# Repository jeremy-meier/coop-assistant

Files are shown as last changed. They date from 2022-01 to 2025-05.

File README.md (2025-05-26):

# Coop Assistant
An ESPHome based automatic chicken coop door integrated with Home Assistant

The Coop Assistant project has the following features:
* Integrated DHT22 temperature and humidity sensor
* Integrated VEML7700 ambient light sensor to enable automatic open/close of coop door
* Two inputs for reed relay door sensors - I use these for the nesting box and larger door in our coop
* Motor drive output for controlling a smaller door ('chicken door') via a linear actuator
  * This is integrated with Home Assisstant using a Cover component.  The ADS1115 Analog to Digital converter senses current in each leg of the H-bridge drive to determine when the door is closed.
  * Home Assistant can be used to configure manual operation of the chicken door, or automatic mode can be used to determine the lighting level when the door should be opened or closed.
* Output for connecting a 12V LED strip for coop lighting
* Inputs for connecting switches for manual Open/Close/Stop operations

See https://github.com/jeremy-meier/coop-assistant for additional documentation.

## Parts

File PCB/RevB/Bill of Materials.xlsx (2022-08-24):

Part | Value | Device | Package | Description | CATEGORY | CREATED_BY | DIGIKEY_PARTNO | MANUFACTURER | MPN | OPERATING_TEMP | PACKAGE | PART_STATUS | POPULARITY | PROD_ID | RATING | ROHS_COMPLIANT | SERIES | SPICEPREFIX | SUB-CATEGORY | THERMALLOSS | TOLERANCE | TP_SIGNAL_NAME | TYPE | VALUE | VOLTAGE
C1 | 220u | CPOLRAD6.3X8 | CAPPRD250W50D630H800B | Radial Solid Polymer Aluminum Capacitors |  |  |  |  |  |  |  |  |  |  |  |  |  |  |  |  |  |  |  |  | 16V
C2 | 100u | CPOLRAD8X12 | CAPPRD350W60D800H1200B | Kemet Radial Solid Polymer Aluminum Capacitors |  |  |  |  |  |  |  |  |  |  |  |  |  |  |  |  |  |  |  |  | 35V
C3 | 0.1u | C-EUC0805 |  | 0.1uF 100V Ceramic
C4 | 1.0uF | 1.0UF-0805-25V-10% | 805 | 1¬µF ceramic capacitors |  |  |  |  |  |  |  |  |  | CAP-08064 |  |  |  |  |  |  |  |  |  | 1.0uF
C6 | 0.1u | 1.0UF-0603-16V-10% | 603 | 1¬µF ceramic capacitors |  |  |  |  |  |  |  |  |  | CAP-00868 |  |  |  |  |  |  |  |  |  | 1.0uF
C7 | 1.0u | 1.0UF-0805-25V-10% | 805 | 1¬µF ceramic capacitors |  |  |  |  |  |  |  |  |  | CAP-08064 |  |  |  |  |  |  |  |  |  | 1.0uF
C8 | 0.1u | 1.0UF-0603-16V-10% | 603 | 1¬µF ceramic capacitors |  |  |  |  |  |  |  |  |  | CAP-00868 |  |  |  |  |  |  |  |  |  | 1.0uF
C9 | 1.0u | 1.0UF-0805-25V-10% | 805 | 1¬µF ceramic capacitors |  |  |  |  |  |  |  |  |  | CAP-08064 |  |  |  |  |  |  |  |  |  | 1.0uF
C10 | 0.1u | 1.0UF-0603-16V-10% | 603 | 1¬µF ceramic capacitors |  |  |  |  |  |  |  |  |  | CAP-00868 |  |  |  |  |  |  |  |  |  | 1.0uF
C11 | 1.0u | 1.0UF-0805-25V-10% | 805 | 1¬µF ceramic capacitors |  |  |  |  |  |  |  |  |  | CAP-08064 |  |  |  |  |  |  |  |  |  | 1.0uF
C12 | 0.1u | 1.0UF-0603-16V-10% | 603 | 1¬µF ceramic capacitors |  |  |  |  |  |  |  |  |  | CAP-00868 |  |  |  |  |  |  |  |  |  | 1.0uF
C13 | 10u | 1.0UF-0805-25V-(+80/-20%) | 805 | 1¬µF ceramic capacitors |  |  |  |  |  |  |  |  |  | CAP-11625 |  |  |  |  |  |  |  |  |  | 1.0uF
C14 | 220n | 1.0UF-0805-25V-(+80/-20%) | 805 | 1¬µF ceramic capacitors |  |  |  |  |  |  |  |  |  | CAP-11625 |  |  |  |  |  |  |  |  |  | 1.0uF
C15 | 220n | 1.0UF-0805-25V-(+80/-20%) | 805 | 1¬µF ceramic capacitors |  |  |  |  |  |  |  |  |  | CAP-11625 |  |  |  |  |  |  |  |  |  | 1.0uF
C16 | 100u | CPOLRAD8X12 | CAPPRD350W60D800H1200B | Kemet Radial Solid Polymer Aluminum Capacitors |  |  |  |  |  |  |  |  |  |  |  |  |  |  |  |  |  |  |  |  | 35V
C17 | 0.1u | 1.0UF-0603-16V-10% | 603 | 1¬µF ceramic capacitors |  |  |  |  |  |  |  |  |  | CAP-00868 |  |  |  |  |  |  |  |  |  | 1.0uF
C18 | 0.1u | 1.0UF-0603-16V-10% | 603 | 1¬µF ceramic capacitors |  |  |  |  |  |  |  |  |  | CAP-00868 |  |  |  |  |  |  |  |  |  | 1.0uF
C19 | 0.1u | 1.0UF-0603-16V-10% | 603 | 1¬µF ceramic capacitors |  |  |  |  |  |  |  |  |  | CAP-00868 |  |  |  |  |  |  |  |  |  | 1.0uF
C20 | 0.1u | C-EUC0805 | C0805 | CAPACITOR, European symbol |  |  |  |  |  |  |  |  | 88 |  |  |  |  | C
C21 | 10n | C-EUC0805 | C0805 | CAPACITOR, European symbol |  |  |  |  |  |  |  |  | 88 |  |  |  |  | C
C22 | 0.1u | 1.0UF-0603-16V-10% | 603 | 1¬µF ceramic capacitors |  |  |  |  |  |  |  |  |  | CAP-00868 |  |  |  |  |  |  |  |  |  | 1.0uF
C23 | 0.1u | 1.0UF-0603-16V-10% | 603 | 1¬µF ceramic capacitors |  |  |  |  |  |  |  |  |  | CAP-00868 |  |  |  |  |  |  |  |  |  | 1.0uF
C24 | 100u | CPOLRAD8X12 | CAPPRD350W60D800H1200B | Kemet Radial Solid Polymer Aluminum Capacitors |  |  |  |  |  |  |  |  |  |  |  |  |  |  |  |  |  |  |  |  | 35V
C26 | 1.0u | 1.0UF-0805-25V-10% | 805 | 1¬µF ceramic capacitors |  |  |  |  |  |  |  |  |  | CAP-08064 |  |  |  |  |  |  |  |  |  | 1.0uF
C27 | 1.0uF | 1.0UF-0805-25V-10% | 805 | 1¬µF ceramic capacitors |  |  |  |  |  |  |  |  |  | CAP-08064 |  |  |  |  |  |  |  |  |  | 1.0uF
C28 | 100u | CPOLRAD8X12 | CAPPRD350W60D800H1200B | Kemet Radial Solid Polymer Aluminum Capacitors |  |  |  |  |  |  |  |  |  |  |  |  |  |  |  |  |  |  |  |  | 35V
D1 | SS2FL4 | SS2FL4 | SMF | SCHOTTKY DIODE, 40V/2A
D2 | RS1A-E3/61T | DIODESMA | SMADIODE | Diode
D3 | RS1A-E3/61T | DIODESMA | SMADIODE | Diode
D4 | MBRA340T3 | MBRA340T3 | SMA | Surface Mount Schottky Power Rectifier |  |  |  |  |  |  |  |  | 9
D5 | 18V | ZENER-DIODESOT23 | SOT23 | Z-Diode |  |  |  |  |  |  |  |  | 3
F1 | 375mA | 494SERIESFUSE | 603
F3 | 3A | 154_OMNIBLOKF154 | FUSM9750X381N
IC1 | 74LVC1G06DBV | 74LVC1G06DBV | SOT23-5 | Single Inverter Buffer/Driver With Open-Drain Output |  |  |  |  |  |  |  |  | 0
IC2 | 74LVC1G06DBV | 74LVC1G06DBV | SOT23-5 | Single Inverter Buffer/Driver With Open-Drain Output |  |  |  |  |  |  |  |  | 0
L1 | 180u | MSS1278 | INDM120120X780N | SMT Power Inductors
L2 | 10uH | COILCRAFT_MSD1260 | COILCRAFT_MSD1260 | Shielded Coupled Inductors
L3 | 10u | MSS1278 | INDM120120X780N | SMT Power Inductors
LED1 |  | LEDCHIP-LED0805 | CHIP-LED0805 | LED
LED2 |  | LEDCHIP-LED0805 | CHIP-LED0805 | LED
LED3 |  | LEDCHIP-LED0805 | CHIP-LED0805 | LED
Q1 | IRFR4105 | IRFR4105 | TO252 | MOSFET 55V 1 N-CH HEXFET 45mOhms 22.7nC
Q2 | IRFR4105 | IRFR4105 | TO252 | MOSFET 55V 1 N-CH HEXFET 45mOhms 22.7nC
Q3 | IRFR4105 | IRFR4105 | TO252 | MOSFET 55V 1 N-CH HEXFET 45mOhms 22.7nC
Q4 | IRFR4105 | IRFR4105 | TO252 | MOSFET 55V 1 N-CH HEXFET 45mOhms 22.7nC
Q5 | IRFR4105 | IRFR4105 | TO252 | MOSFET 55V 1 N-CH HEXFET 45mOhms 22.7nC
Q6 | X0202MN_5BA4 | X0202MN_5BA4 | SOT-223 | SCR 600V 1.25A SOT-223
R1 | 22 | R-US_R0805 | R0805 | RESISTOR, American symbol
R2 | 1k | R-US_R0805 | R0805 | RESISTOR, American symbol
R3 | 4.7k | R-US_R0805 | R0805 | RESISTOR, American symbol
R4 | 100 | R-US_R0805 | R0805 | RESISTOR, American symbol
R5 | 1k | R-US_R0805 | R0805 | RESISTOR, American symbol
R16 | 0 | R-US_R0805 | R0805 | RESISTOR, American symbol
R17 | 1k | R-US_R0805 | R0805 | RESISTOR, American symbol
R18 | 1k | R-US_R0805 | R0805 | RESISTOR, American symbol
R19 | 0 | R-US_R0805 | R0805 | RESISTOR, American symbol
R20 | 1k | R-US_R0805 | R0805 | RESISTOR, American symbol
R21 | 1k | R-US_R0805 | R0805 | RESISTOR, American symbol
R22 | 22 | R-US_R0805 | R0805 | RESISTOR, American symbol
R23 | 10k | R-US_R0805 | R0805 | RESISTOR, American symbol
R24 | 47k | R-US_R0805 | R0805 | RESISTOR, American symbol
R25 | 4.7k | R-US_R0805 | R0805 | RESISTOR, American symbol
R26 | 50m | R-US_R2512 | R2512 | RESISTOR, American symbol
R27 | 50m | R-US_R2512 | R2512 | RESISTOR, American symbol
R28 | 4.7k | R-US_R0805 | R0805 | RESISTOR, American symbol
R29 | 4.7k | R-US_R0805 | R0805 | RESISTOR, American symbol
R30 | 1.5k | R-US_R0805 | R0805 | RESISTOR, American symbol
R31 | 1k | R-US_R0805 | R0805 | RESISTOR, American symbol
R32 | 47k | R-US_R0805 | R0805 | RESISTOR, American symbol
R33 | 100m | R-US_CHIP-1206(3216-METRIC) | RESC3216X70 | Resistor Fixed - ANSI | Resistor |  |  |  |  |  |  |  |  |  |  |  |  |  | Fixed
R34 | 1k | R-US_R0805 | R0805 | RESISTOR, American symbol
R35 | 100 | R-US_R2512 | R2512 | RESISTOR, American symbol
R39 | 0 | R-US_R0805 | R0805 | RESISTOR, American symbol
R40 | 22 | R-US_R0805 | R0805 | RESISTOR, American symbol
R41 | 22 | R-US_R0805 | R0805 | RESISTOR, American symbol
R42 | 22 | R-US_R0805 | R0805 | RESISTOR, American symbol
R43 | 22 | R-US_R0805 | R0805 | RESISTOR, American symbol
R44 | 1k | R-US_R0805 | R0805 | RESISTOR, American symbol
R45 | 1k | R-US_R0805 | R0805 | RESISTOR, American symbol
T1 | BC847 | BC847 | SOT23 | NPN TRANSISTOR |  |  |  |  |  |  |  |  | 5
T2 | BC847 | BC847 | SOT23 | NPN TRANSISTOR |  |  |  |  |  |  |  |  | 5
T3 | BC857A | BC857A | SOT23-BEC | 65 V, 100 mA PNP general-purpose transistor
TP1 | TPTP15SQ | TPTP15SQ | TP15SQ | Test pad |  |  |  |  |  |  |  |  | 0
TP2 | TPTP15SQ | TPTP15SQ | TP15SQ | Test pad |  |  |  |  |  |  |  |  | 0
TP3 | TPTP15SQ | TPTP15SQ | TP15SQ | Test pad |  |  |  |  |  |  |  |  | 0
TP4 | TPTP15SQ | TPTP15SQ | TP15SQ | Test pad |  |  |  |  |  |  |  |  | 0
TP5 | TPTP15SQ | TPTP15SQ | TP15SQ | Test pad |  |  |  |  |  |  |  |  | 0
TP6 | TPTP15SQ | TPTP15SQ | TP15SQ | Test pad |  |  |  |  |  |  |  |  | 0
TP7 | TPTP15SQ | TPTP15SQ | TP15SQ | Test pad |  |  |  |  |  |  |  |  | 0
TP8 | TPTP15SQ | TPTP15SQ | TP15SQ | Test pad |  |  |  |  |  |  |  |  | 0
TP9 | TPTP15SQ | TPTP15SQ | TP15SQ | Test pad |  |  |  |  |  |  |  |  | 0
TP10 | TPTP15SQ | TPTP15SQ | TP15SQ | Test pad |  |  |  |  |  |  |  |  | 0
TP11 | TPTP15SQ | TPTP15SQ | TP15SQ | Test pad |  |  |  |  |  |  |  |  | 0
TP12 | TPTP15SQ | TPTP15SQ | TP15SQ | Test pad |  |  |  |  |  |  |  |  | 0
TP13 | TPTP15SQ | TPTP15SQ | TP15SQ | Test pad |  |  |  |  |  |  |  |  | 0
U1 | DHT22 | RHT03_DHT-22_AM2302RA | RHT03_DHT-22/RA | RHT03 / DHT-22 / AM2302 |  |  |  |  |  |  |  |  |  | SEN-10167
U2 | ESP8266_NODEMCU | ESP8266_NODEMCU | NODEMCUESP8266 | ESP8266 NODEMCU board.
U3 | HIP4082IPZ | HIP4082IPZ | DIP762W53P254L1969H508Q16B
U4 | MIC4575-5.0WU | MIC4575-5.0WU | TO263-5 | MIC4575
U5 | LP2980AIM5-3.3 | LP2980AIM5-3.3 | SOT23-5 | Micropower 50-mA Ultra-Low-Dropout Regulator
U6 | ADS1115 | ADS1115 | HDRV10W64P254_1X10_2800X508X838B
U7 | VEML7700 | VEML7700 | VEML7700
U8 | SFH3716 | SFH3716 | 805 | Silicon NPN Phototransistor with VŒª Characteristics
U9 | ADS1115IDGST | ADS1115IDGST | 10VSSOP
X1 | MKDSN1,5/2-5,08 | MKDSN1,5/2-5,08 | MKDSN1,5/2-5,08 | MKDSN 1,5/ 2-5,08 Printklemme |  |  |  |  |  |  |  |  | 14
X2 | MKDSN1,5/8-5,08 | MKDSN1,5/8-5,08 | MKDSN1,5/8-5,08 | MKDSN 1,5/ 8-5,08 Printklemme |  |  |  |  |  |  |  |  | 1
X3 | MKDSN1,5/8-5,08 | MKDSN1,5/8-5,08 | MKDSN1,5/8-5,08 | MKDSN 1,5/ 8-5,08 Printklemme |  |  |  |  |  |  |  |  | 1
X4 | MKDSN1,5/8-5,08 | MKDSN1,5/8-5,08 | MKDSN1,5/8-5,08 | MKDSN 1,5/ 8-5,08 Printklemme |  |  |  |  |  |  |  |  | 1

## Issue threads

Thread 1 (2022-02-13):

Buck converter unstable due to insufficient ESR in output capacitor

jeremy-meier, 2022-02-13:
The MIC4575 buck controller is unstable when using the original values in the Rev A schematic.  Adding 100mOhm of ESR in series with the capacitor moves the zero lower in frequency and provides additional phase margin to make converter stable.

jeremy-meier, 2022-08-24:
R33 Added in Rev B PCB.

Closed 2022-08-24.

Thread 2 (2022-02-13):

Need additional bulk capacitance

jeremy-meier, 2022-02-13:
Some additional bulk capacitance is needed next to the H-bridge switches to help with the fast transients of turning the motor on/off.  Consider adding a couple of the 100uF caps that are already used on the buck converter input.

jeremy-meier, 2022-08-24:
C24, C16, C28 added to rev B PCB.

Closed 2022-08-24.

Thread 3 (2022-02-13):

Some additional pull up/downs needed to utilize GPIO2/GPIO15 pins

jeremy-meier, 2022-02-13:
A couple of pins are being used that need to be pulled to specific levels, otherwise the device fails to boot.  The following modifications should be made based on the following document:
https://randomnerdtutorials.com/esp8266-pinout-reference-gpio

* GPIO2/LIGHT_PWM - Needs to be pulled high otherwise the device can't boot.  Use a strong pull down, 1k should be fine.
* GPIO15/MOTOR_PWM - Needs to be pulled to ground otherwise the device can't boot.  Use a strong pull down, 1k should be fine.

jeremy-meier, 2022-08-24:
R17 & R34 added to rev B PCB.

Closed 2022-08-24.

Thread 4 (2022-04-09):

Kickback from motor turn off is triggering OVP

jeremy-meier, 2022-04-09:
When the motor turns off, the energy stored in the inductance is being pumped back onto the voltage rail, causing the OVP protection to trip.  To fix this, consider both of the following:
1. Add a snubber circuit across the motor terminals to reduce kickback
2. Put a schottky diode in series with the power feed to the output MOSFETS to prevent kickback from reaching the OVP circuit

The additional bulk capacitance on the output MOSFET power supply should also help reduce this problem.

jeremy-meier, 2022-08-24:
1. Added snubber circuit R35/C3 to rev B
2. Added schottky D6 to rev B
3. Also increased the zener voltage of D5 from 15V to 18V

Closed 2022-08-24.

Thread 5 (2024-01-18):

Use a temperature sensor capable of operating at lower temperatures

jeremy-meier, 2024-01-18:
The DHT22 temperature sensor specs say it should work down to -40C, but it doesn't seem like that's the case.  The sensor is reporting -5000 degrees in home assistant when the temperature drops below freezing.  However humidity seems fine.  Consider using a different temperature sensor.

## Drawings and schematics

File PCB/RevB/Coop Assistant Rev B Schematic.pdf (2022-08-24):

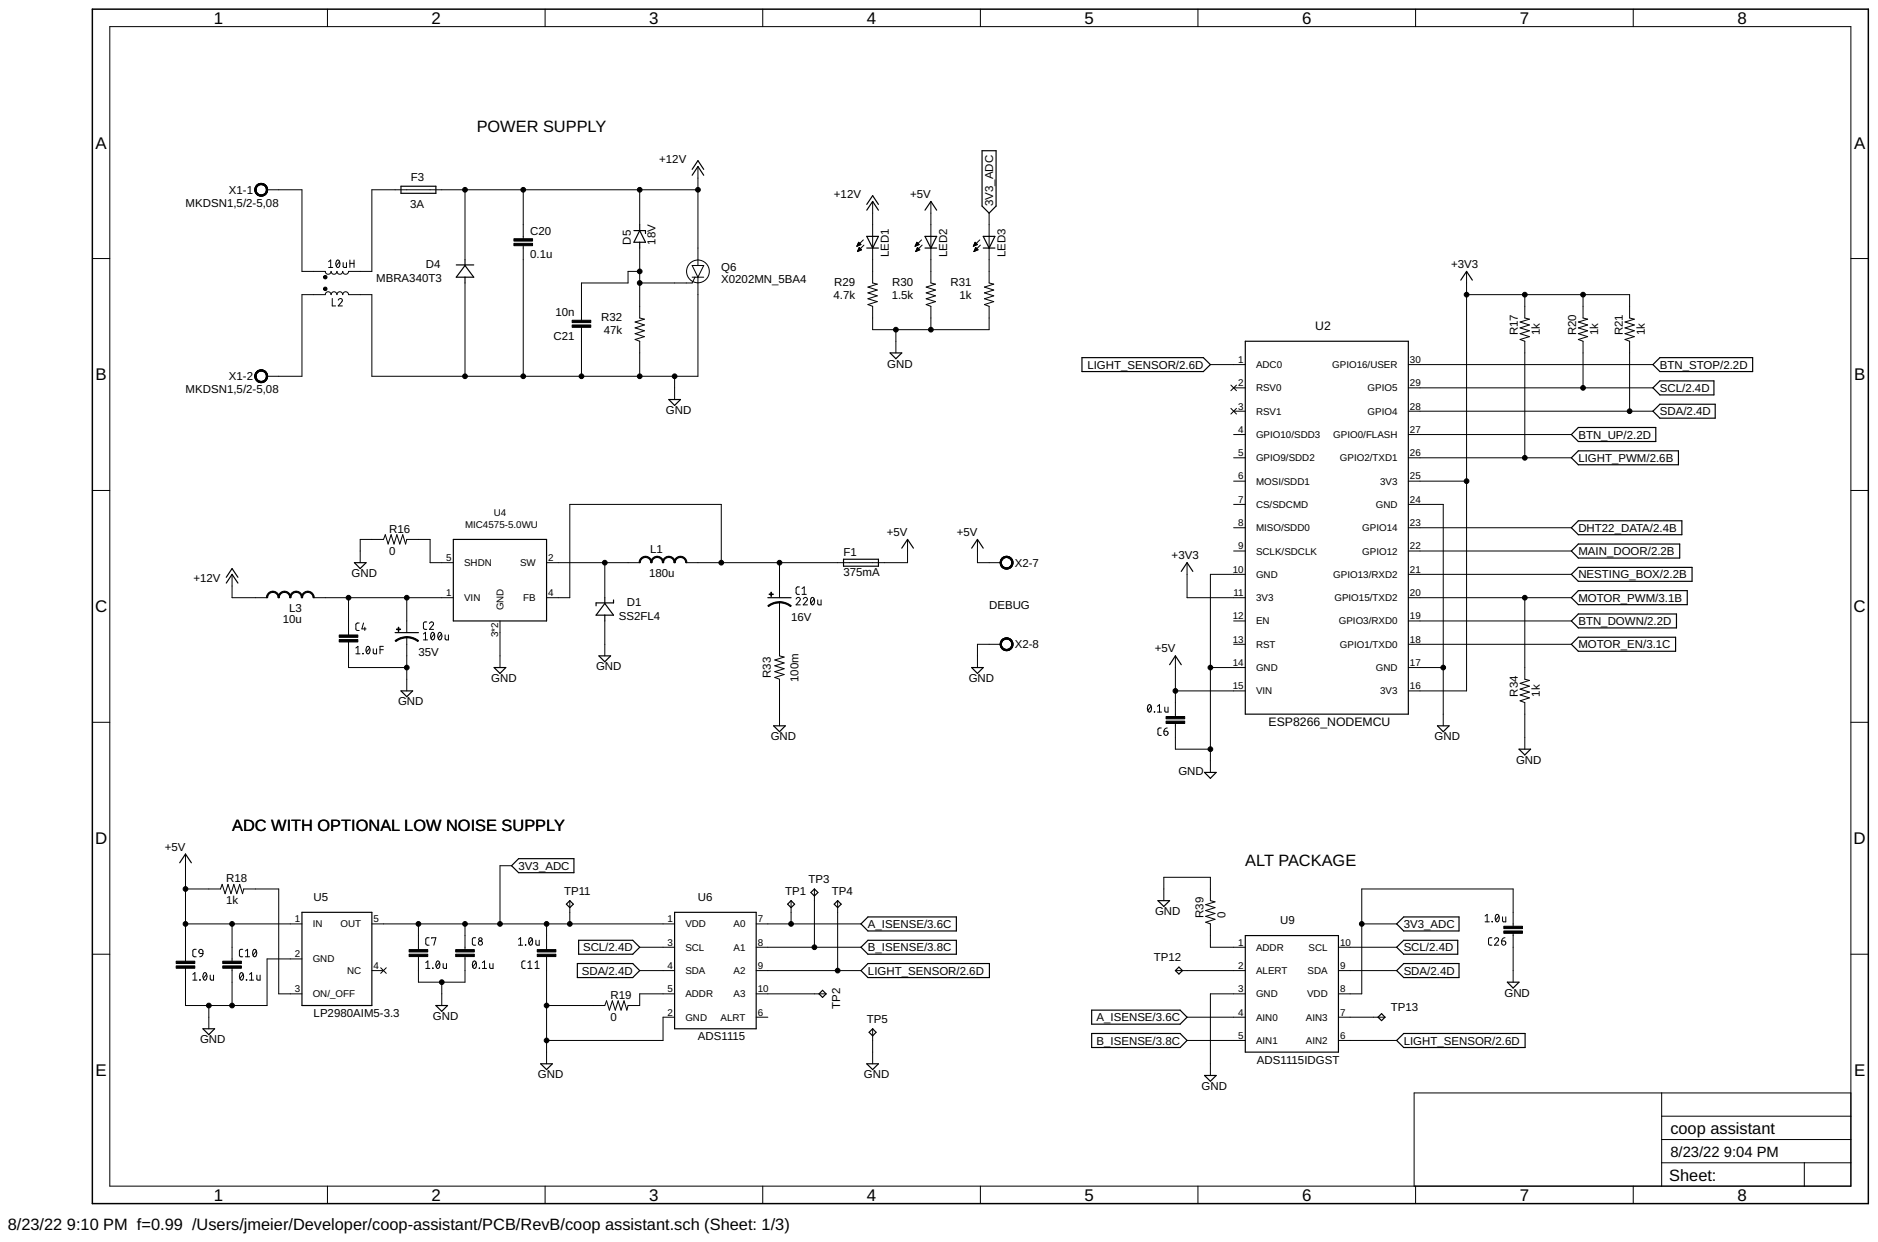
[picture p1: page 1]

ADC WITH OPTIONAL LOW NOISE SUPPLY

8/23/22 9:10 PM f=0.99 /Users/jmeier/Developer/coop-assistant/PCB/RevB/coop assistant.sch (Sheet: 1/3)

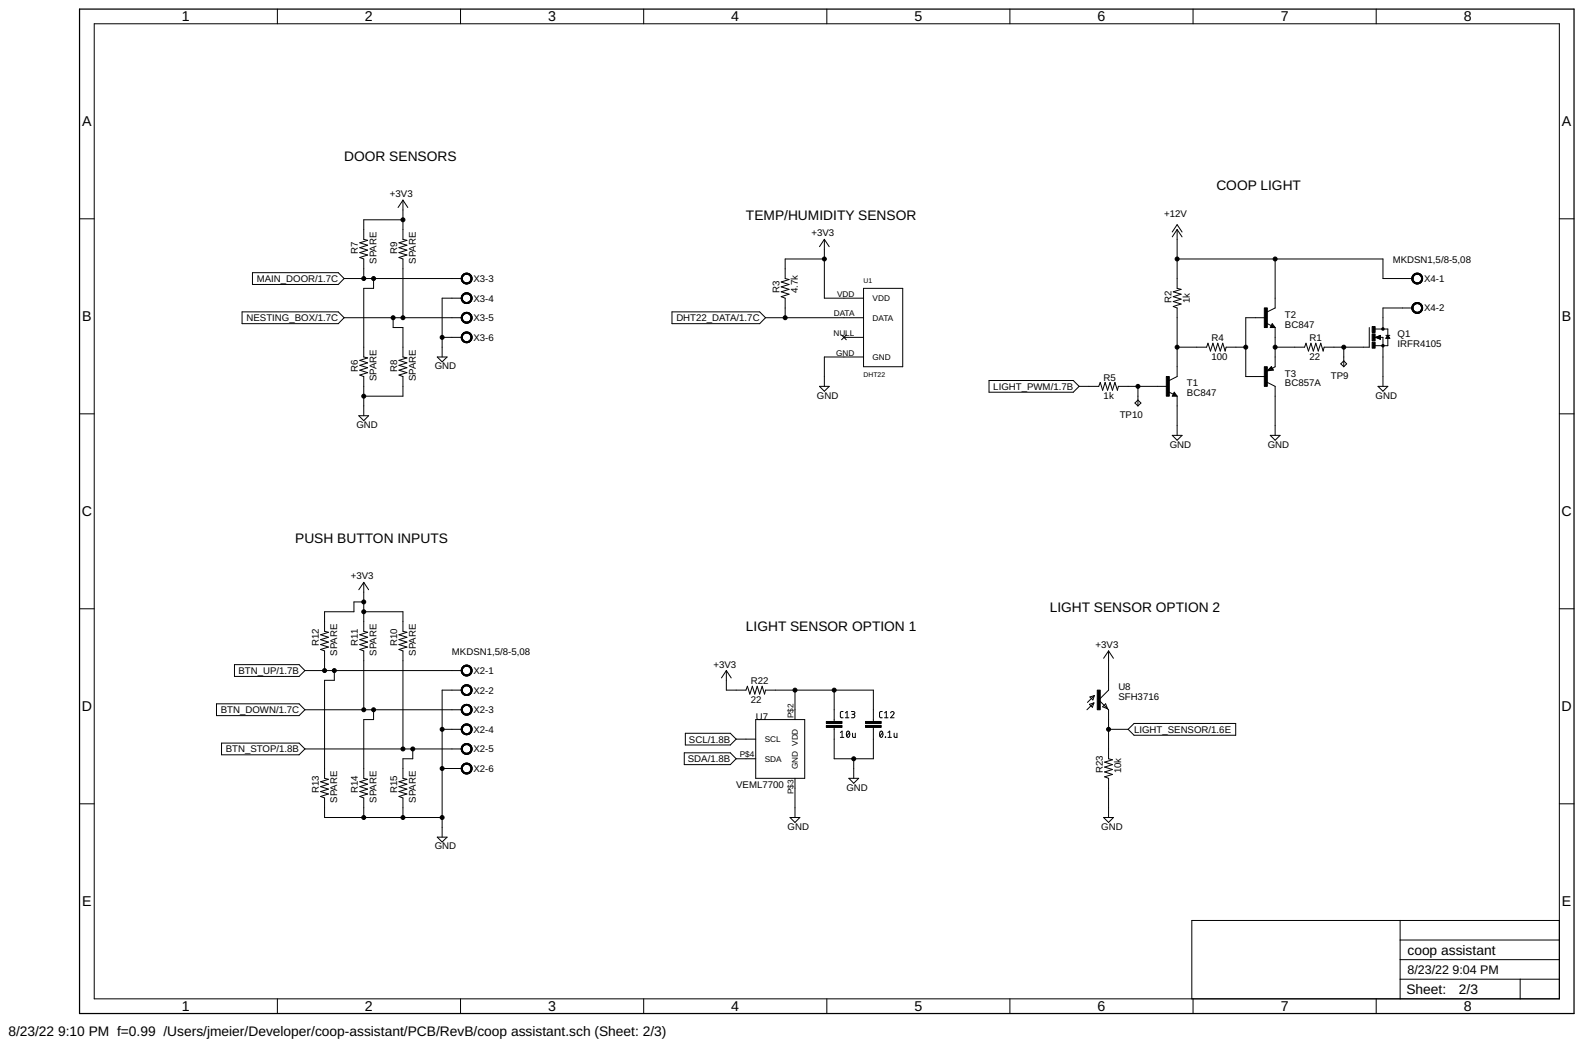
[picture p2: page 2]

8/23/22 9:10 PM f=0.99 /Users/jmeier/Developer/coop-assistant/PCB/RevB/coop assistant.sch (Sheet: 2/3)

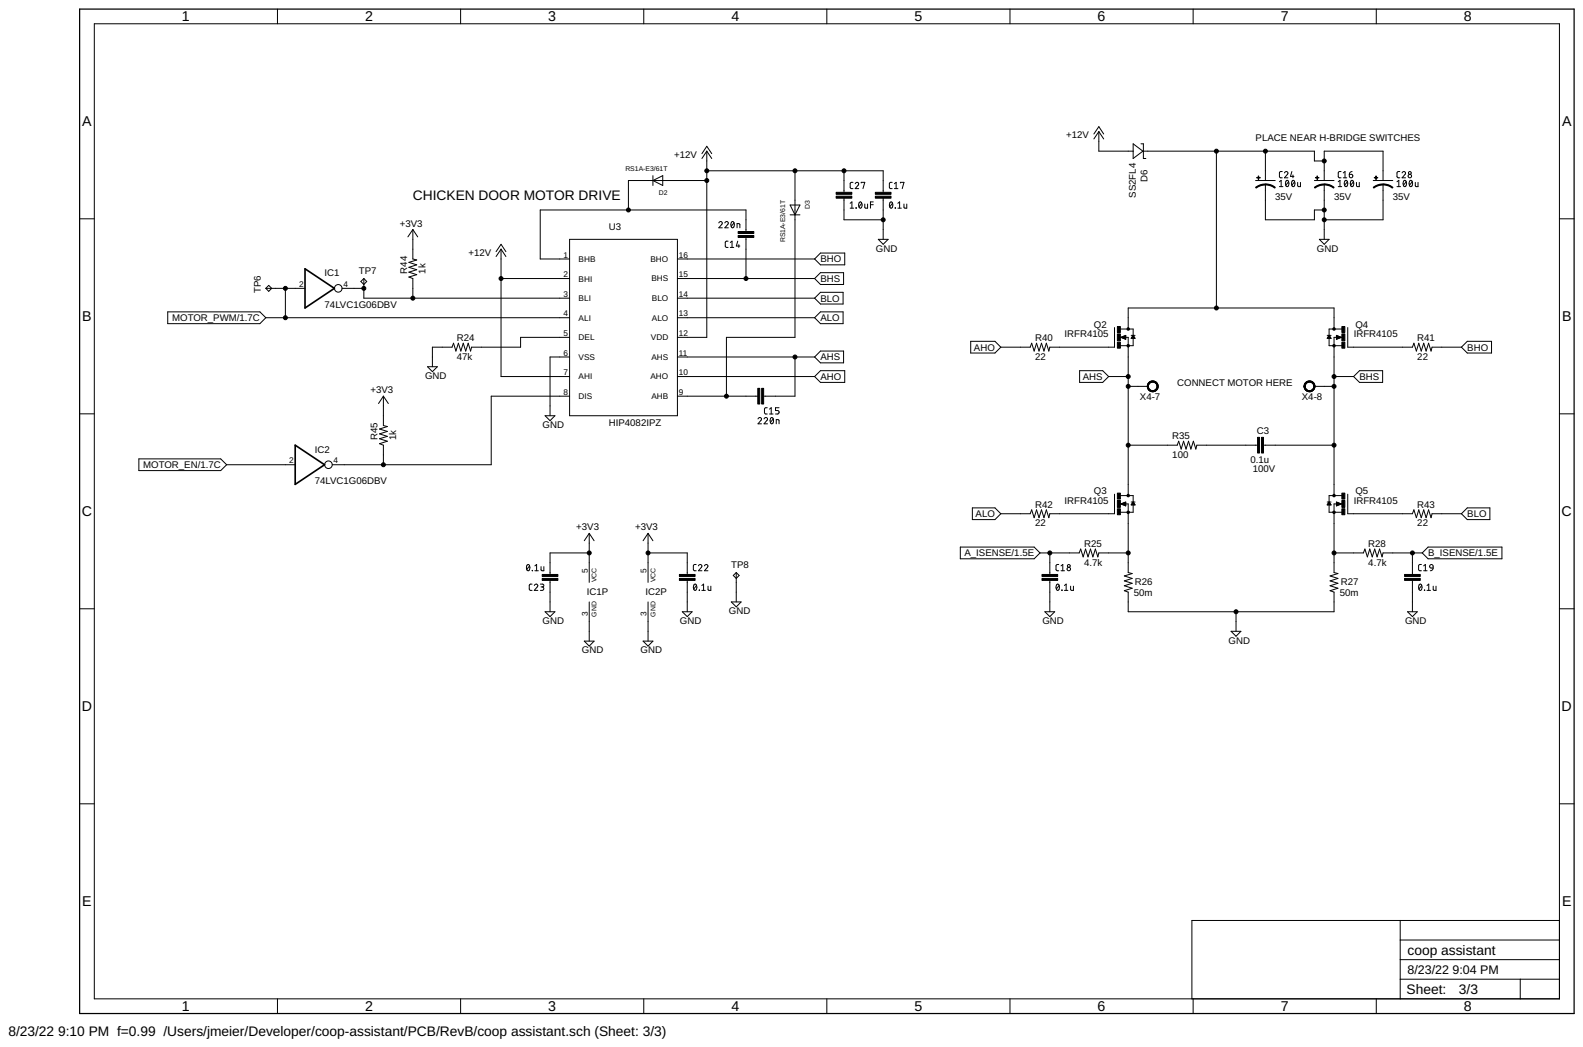
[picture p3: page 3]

PLACE NEAR H-BRIDGE SWITCHES

CHICKEN DOOR MOTOR DRIVE

8/23/22 9:10 PM f=0.99 /Users/jmeier/Developer/coop-assistant/PCB/RevB/coop assistant.sch (Sheet: 3/3)

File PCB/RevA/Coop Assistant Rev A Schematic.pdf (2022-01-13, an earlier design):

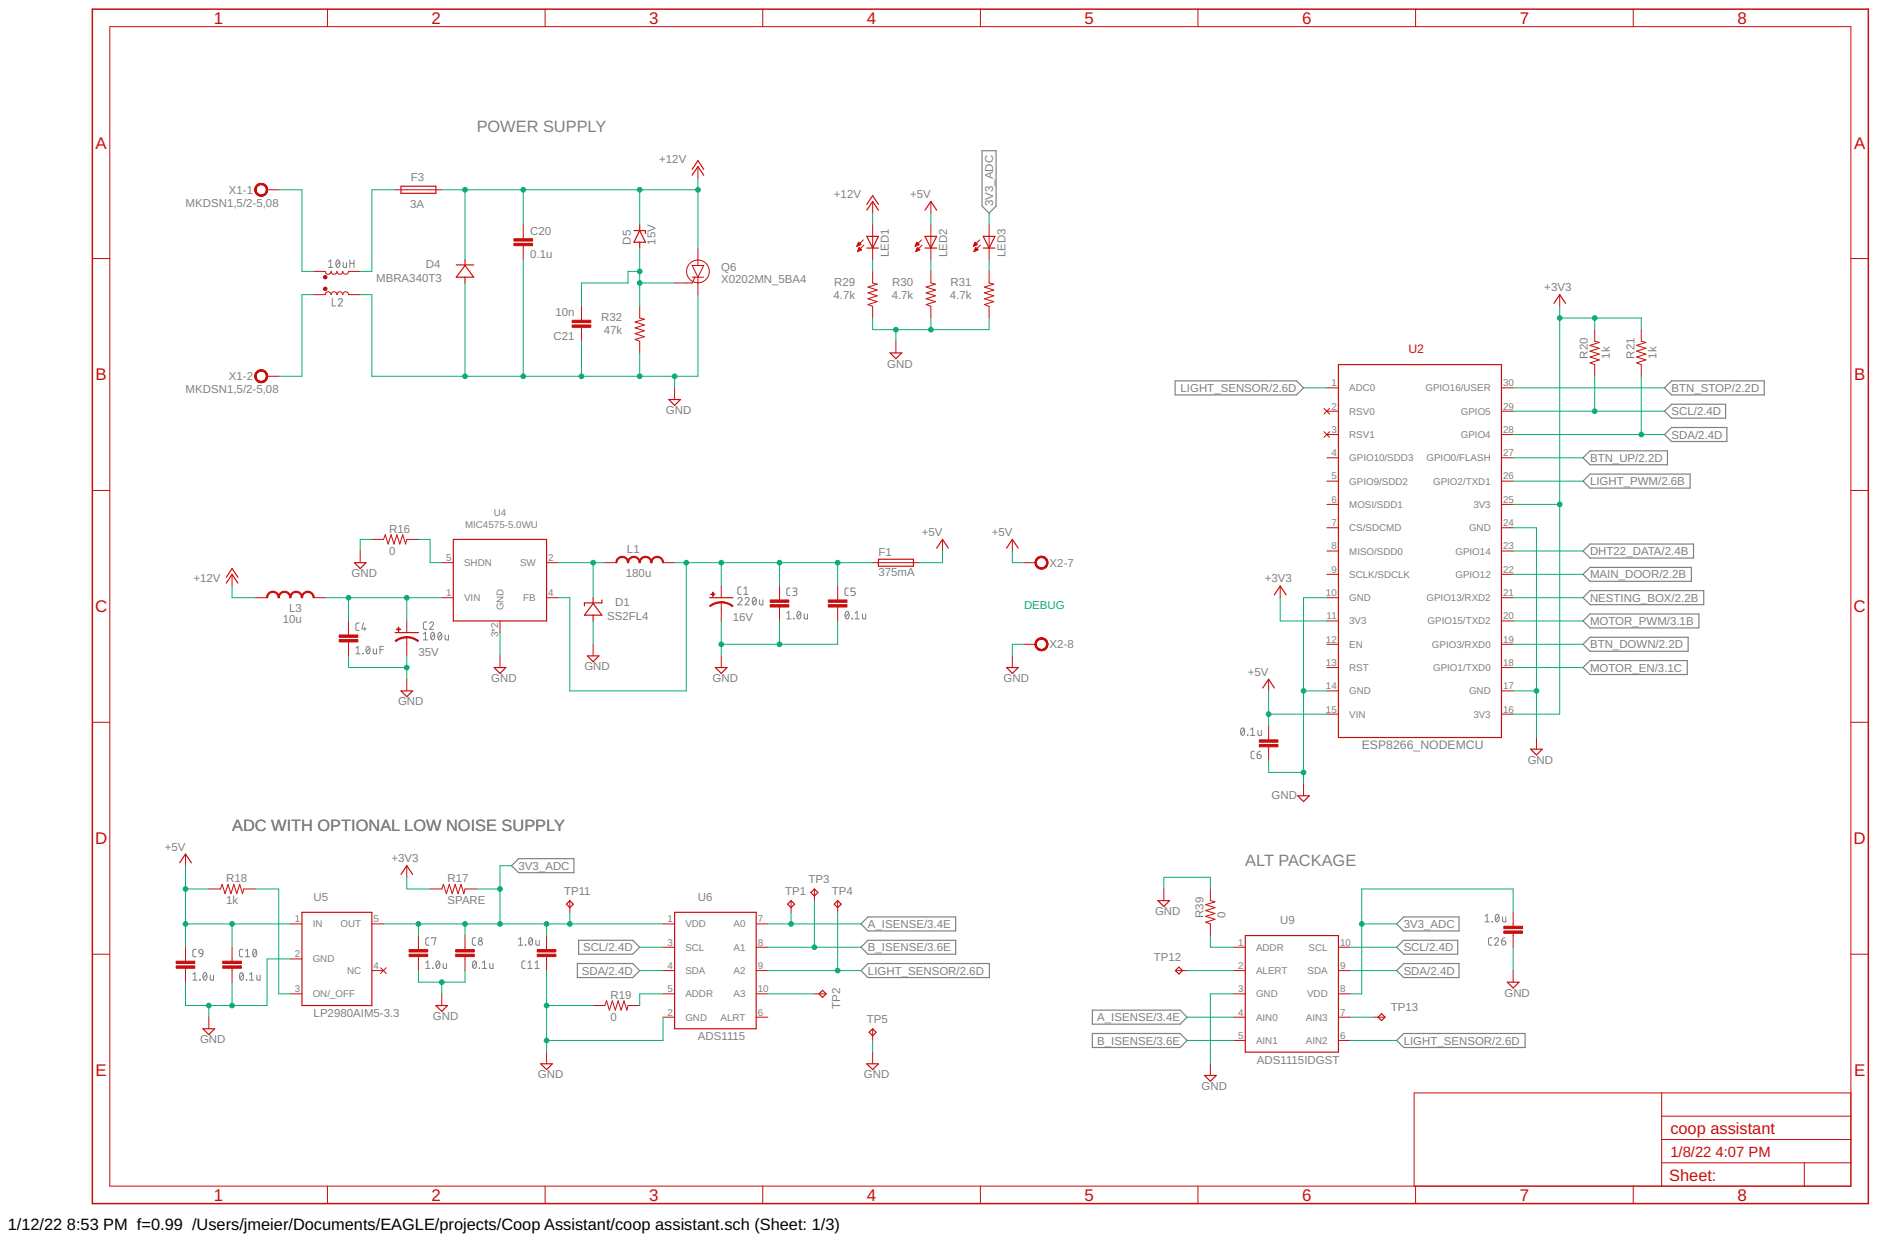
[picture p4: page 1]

ADC WITH OPTIONAL LOW NOISE SUPPLY

1/12/22 8:53 PM f=0.99 /Users/jmeier/Documents/EAGLE/projects/Coop Assistant/coop assistant.sch (Sheet: 1/3)

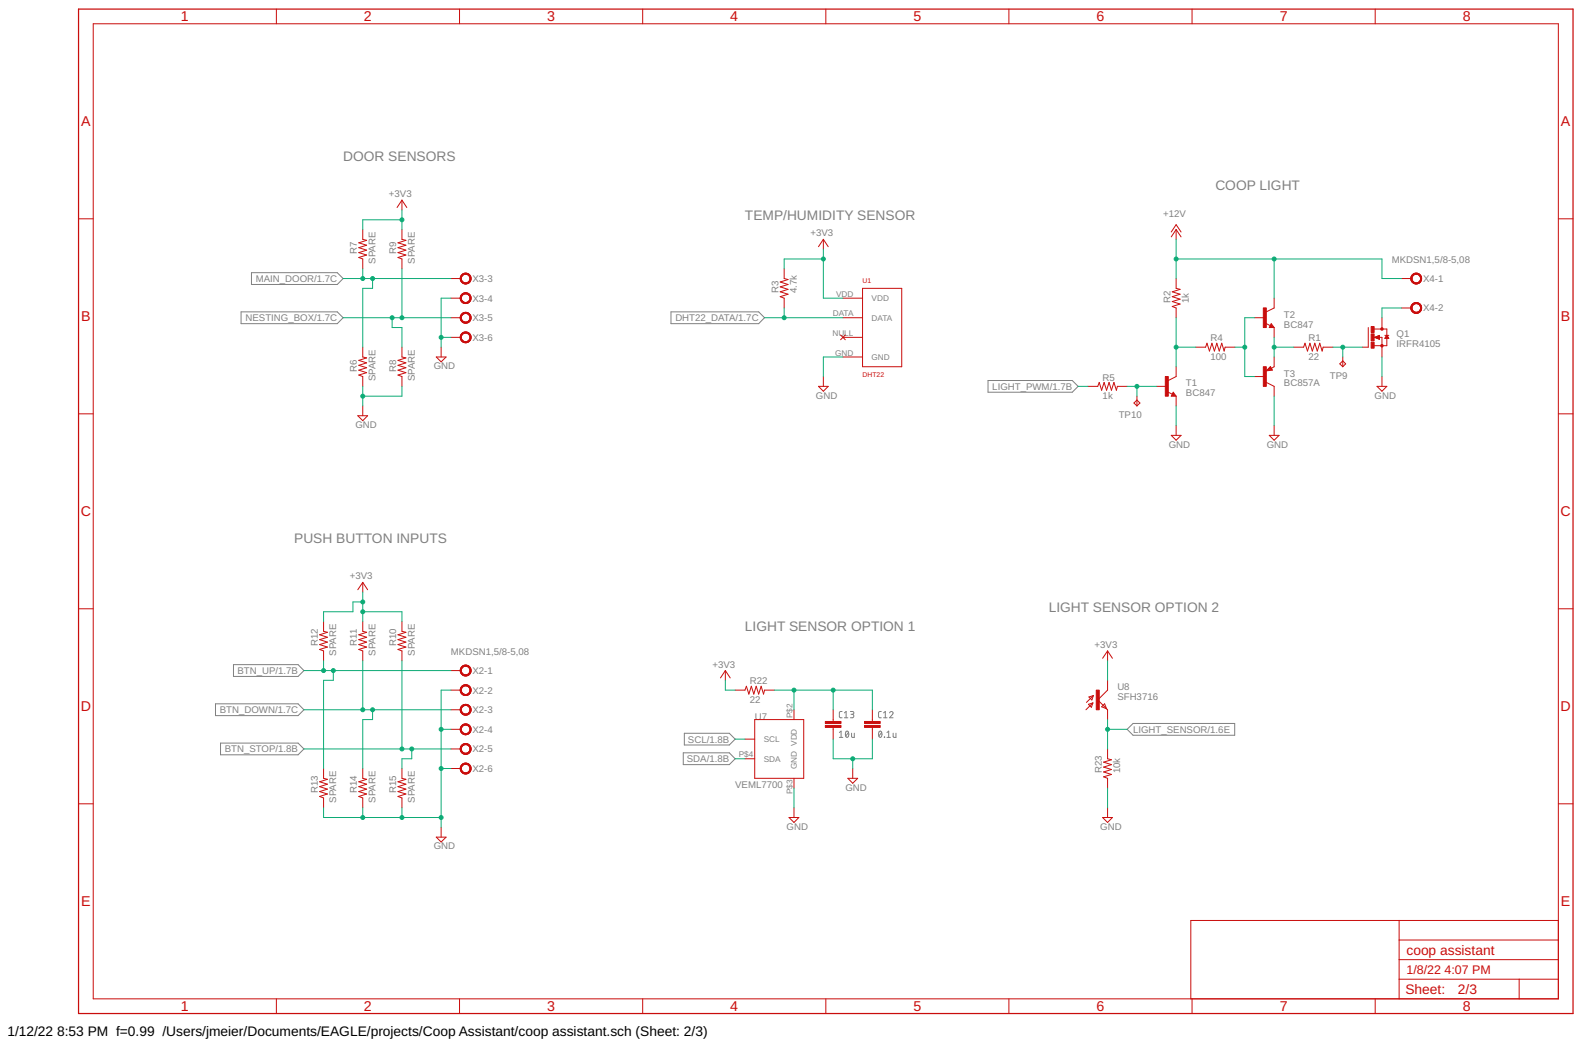
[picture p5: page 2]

1/12/22 8:53 PM f=0.99 /Users/jmeier/Documents/EAGLE/projects/Coop Assistant/coop assistant.sch (Sheet: 2/3)

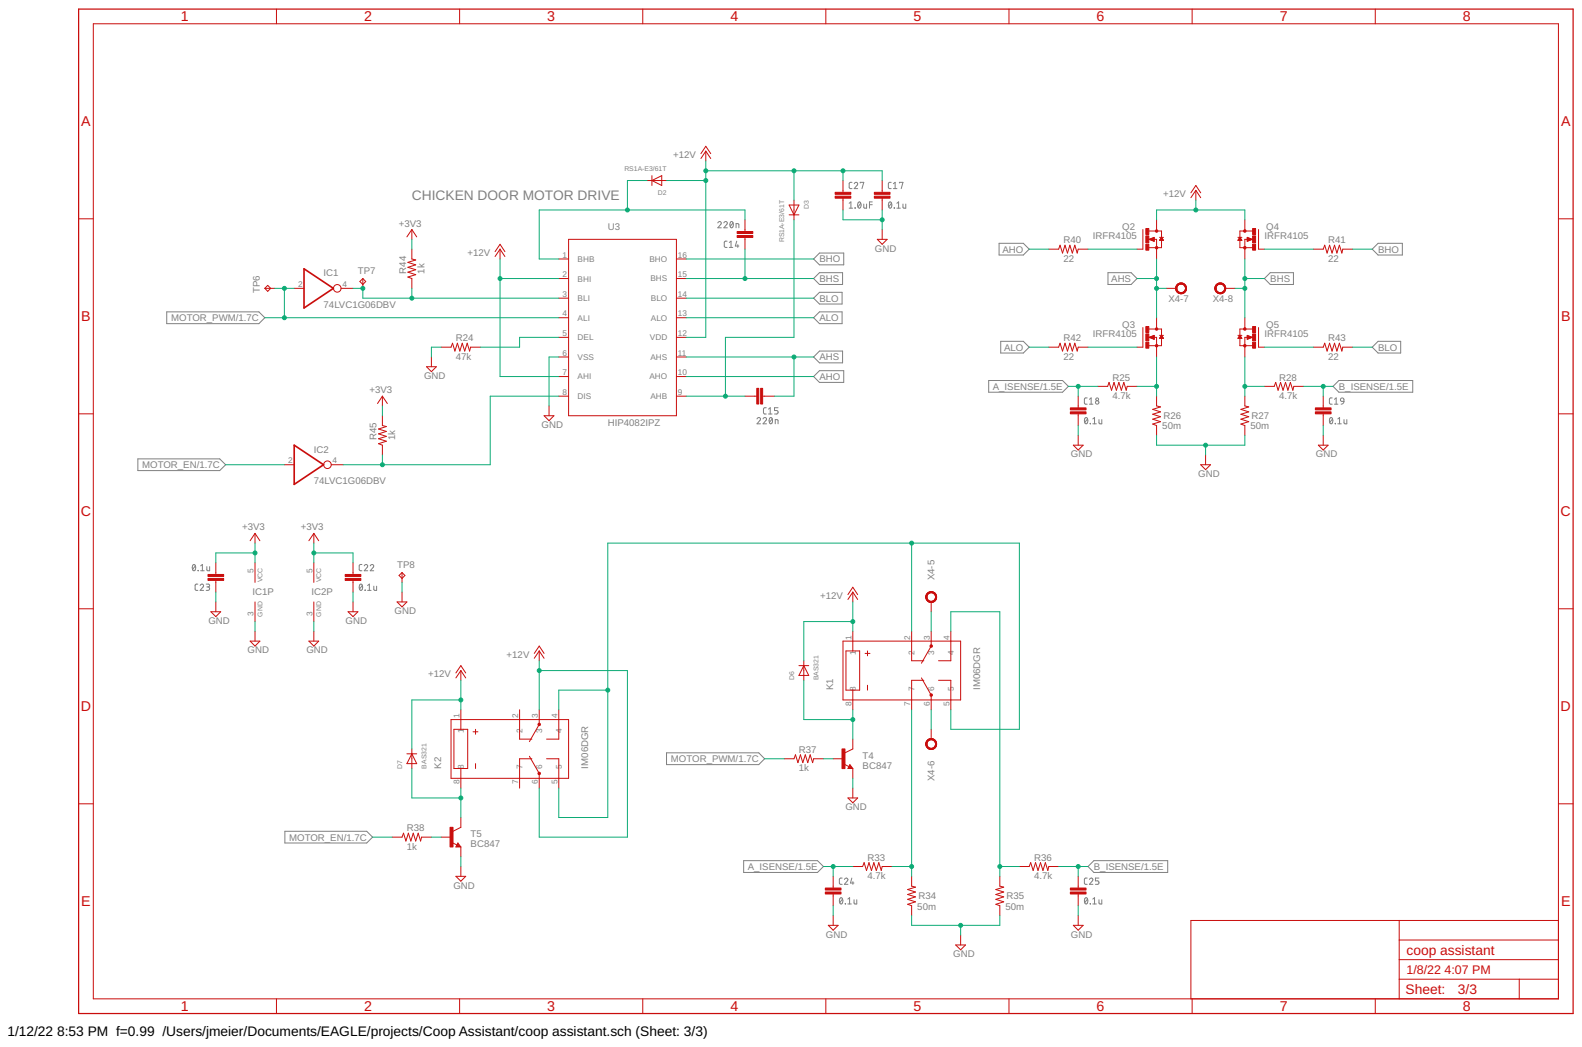
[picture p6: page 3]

CHICKEN DOOR MOTOR DRIVE

1/12/22 8:53 PM f=0.99 /Users/jmeier/Documents/EAGLE/projects/Coop Assistant/coop assistant.sch (Sheet: 3/3)

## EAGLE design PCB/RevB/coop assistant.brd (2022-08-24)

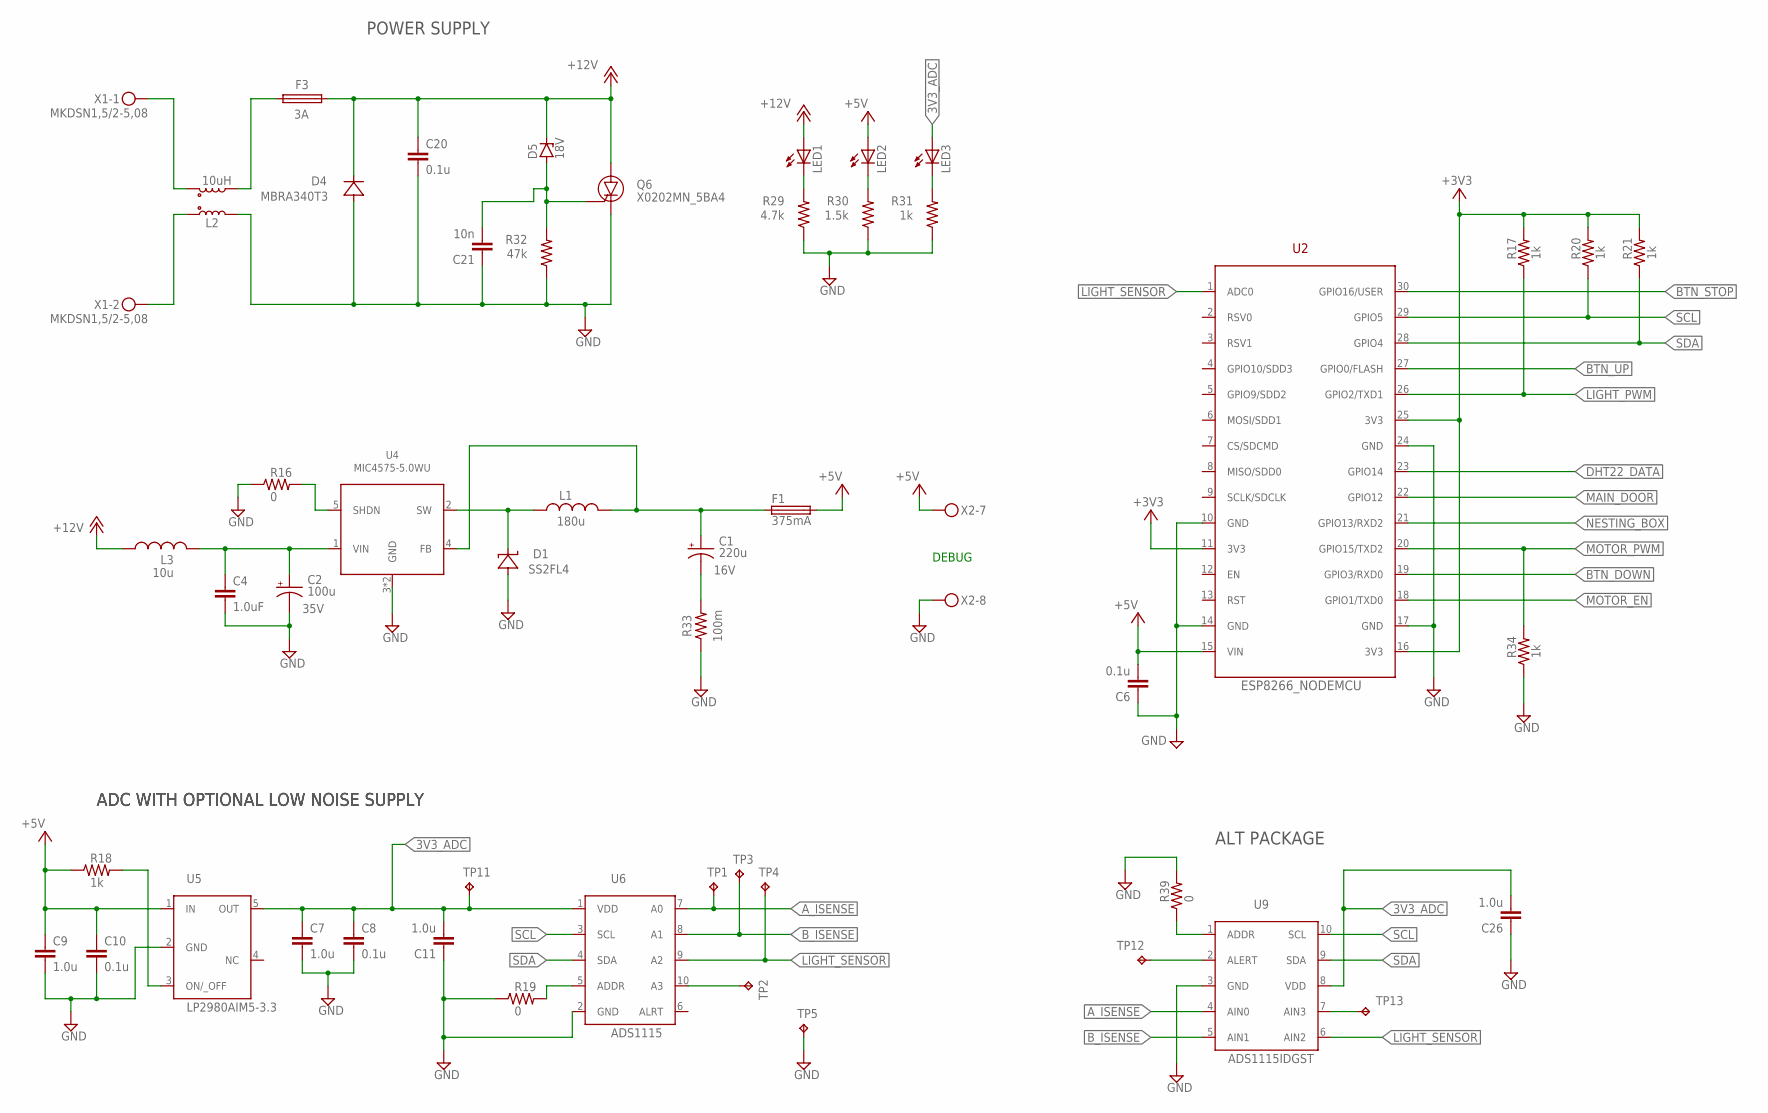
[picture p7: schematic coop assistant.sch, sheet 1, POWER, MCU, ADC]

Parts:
C1: 220u; CAPPRD250W50D630H800B; VOLTAGE 16V
C2: 100u; CAPPRD350W60D800H1200B; VOLTAGE 35V
C4: 1.0uF; 0805
C6, C8, C10: 0.1u; 0603
C7, C9, C11, C26: 1.0u; 0805
C20: 0.1u; C0805
C21: 10n; C0805
D1: SS2FL4; SMF
D4: MBRA340T3; SMA
D5: 18V; SOT23
F1: 375mA; 0603
F3: 3A; FUSM9750X381N
L1: 180u; INDM120120X780N
L2: 10uH; COILCRAFT_MSD1260
L3: 10u; INDM120120X780N
LED1, LED2, LED3: LEDCHIP-LED0805; CHIP-LED0805
Q6: X0202MN_5BA4; SOT-223
R16, R19, R39: 0; R0805
R17, R18, R20, R21, R31, R34: 1k; R0805
R29: 4.7k; R0805
R30: 1.5k; R0805
R32: 47k; R0805
R33: 100m; RESC3216X70
TP1, TP2, TP3, TP4, TP5, TP11, TP12, TP13: TPTP15SQ; TP15SQ
U2: ESP8266_NODEMCU; NODEMCUESP8266
U4: MIC4575-5.0WU; TO263-5
U5: LP2980AIM5-3.3; SOT23-5
U6: ADS1115; HDRV10W64P254_1X10_2800X508X838B
U9: ADS1115IDGST; 10VSSOP
X1: MKDSN1,5/2-5,08
X2: MKDSN1,5/8-5,08

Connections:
3V3_ADC: C7.1, C8.1, C11.2, C26.2, LED3.A, TP11.TP, U5.5 (OUT), U6.1 (VDD), U9.8 (VDD)
5VBUCK_SHDN: R16.2, U4.5 (SHDN)
5VBUCK_SW: D1.K (C), L1.1, U4.2 (SW)
5VBUCK_VIN: C2.POS (+), C4.1, L3.2, U4.1 (VIN)
5VBUCK_VOUT: C1.POS (+), F1.1, L1.2, U4.4 (FB)
5VBUCK_VOUT_ESR: C1.NEG (-), R33.2
+3V3: R17.2, R20.2, R21.2, U2.11 (3V3), U2.16 (3V3), U2.25 (3V3); also elsewhere on the board
+5V: C6.2, C9.1, C10.1, F1.2, LED2.A, R18.1, U2.15 (VIN), U5.1 (IN), X2.7
+12V: C20.1, D4.C, D5.3 (C), F3.2, L3.1, LED1.A, Q6.A, Q6.A1 (A); also elsewhere on the board
+12V_PREFUSE: F3.1, L2.3
ADS1115_ADDR: R19.2, U6.5 (ADDR)
A_ISENSE: TP1.TP, U6.7 (A0), U9.4 (AIN0); also elsewhere on the board
BTN_DOWN: U2.19 (GPIO3/RXD0); also elsewhere on the board
BTN_STOP: U2.30 (GPIO16/USER); also elsewhere on the board
BTN_UP: U2.27 (GPIO0/FLASH); also elsewhere on the board
B_ISENSE: TP3.TP, U6.8 (A1), U9.5 (AIN1); also elsewhere on the board
DHT22_DATA: U2.23 (GPIO14); also elsewhere on the board
GND: C2.NEG (-), C4.2, C6.1, C7.2, C8.2, C9.2, C10.2, C11.1, C20.2, C21.1, C26.1, D1.A, D4.A, L2.4, Q6.K, R16.1, R19.1, R29.1, R30.1, R31.1, R32.1, R33.1, R34.1, R39.2, TP5.TP, U2.10 (GND), U2.14 (GND), U2.17 (GND), U2.24 (GND), U4.3 (GND), U4.6 (GND), U5.2 (GND), U6.2 (GND), U9.3 (GND), X2.8; also elsewhere on the board
LED_3V3_ADC: LED3.C, R31.2
LED_5V: LED2.C, R30.2
LED_12V: LED1.C, R29.2
LIGHT_PWM: R17.1, U2.26 (GPIO2/TXD1); also elsewhere on the board
LIGHT_SENSOR: TP4.TP, U2.1 (ADC0), U6.9 (A2), U9.6 (AIN2); also elsewhere on the board
MAIN_DOOR: U2.22 (GPIO12); also elsewhere on the board
MOTOR_EN: U2.18 (GPIO1/TXD0); also elsewhere on the board
MOTOR_PWM: R34.2, U2.20 (GPIO15/TXD2); also elsewhere on the board
unnamed: TP2.TP, U6.10 (A3)
unnamed: TP12.TP, U9.2 (ALERT)
unnamed: R39.1, U9.1 (ADDR)
unnamed: TP13.TP, U9.7 (AIN3)
NESTING_BOX: U2.21 (GPIO13/RXD2); also elsewhere on the board
SCL: R20.1, U2.29 (GPIO5), U6.3 (SCL), U9.10 (SCL); also elsewhere on the board
SDA: R21.1, U2.28 (GPIO4), U6.4 (SDA), U9.9 (SDA); also elsewhere on the board
VADC_EN: R18.2, U5.3 (ON/_OFF)
VIN+: L2.1, X1.1
VIN-: L2.2, X1.2
VIN_CROWBAR_GATE: C21.2, D5.1 (A), Q6.G, R32.2

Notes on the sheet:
POWER SUPPLY
ADC WITH OPTIONAL LOW NOISE SUPPLY
DEBUG
ALT PACKAGE

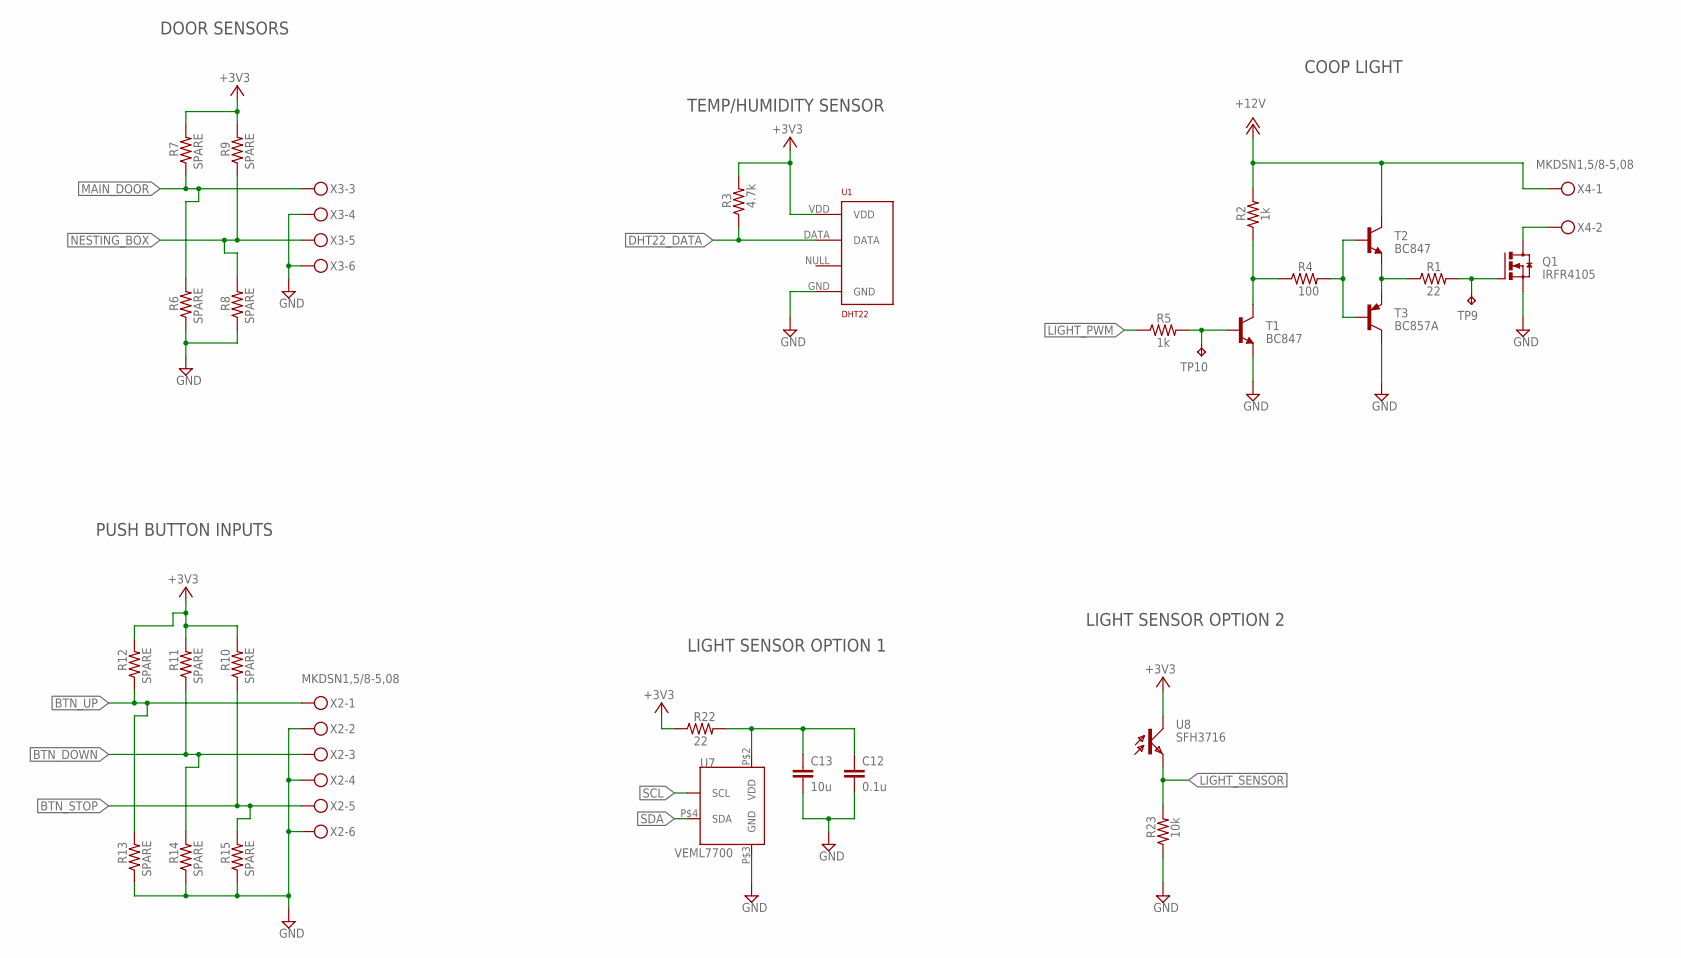
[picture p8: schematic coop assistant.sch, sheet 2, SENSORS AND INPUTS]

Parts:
C12: 0.1u; 0603
C13: 10u; 0805
Q1: IRFR4105; TO252
R1, R22: 22; R0805
R2, R5: 1k; R0805
R3: 4.7k; R0805
R4: 100; R0805
R6, R7, R8, R9, R10, R11, R12, R13, R14, R15: SPARE; R0805
R23: 10k; R0805
T1, T2: BC847; SOT23
T3: BC857A; SOT23-BEC
TP9, TP10: TPTP15SQ; TP15SQ
U1: DHT22; RHT03_DHT-22/RA
U7: VEML7700
U8: SFH3716; 0805
X2, X3, X4: MKDSN1,5/8-5,08

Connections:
+3V3: R3.2, R7.2, R9.2, R10.2, R11.2, R12.2, R22.1, U1.VDD, U8.1 (C); also elsewhere on the board
+12V: R2.2, T2.3 (C), X4.1; also elsewhere on the board
BTN_DOWN: R11.1, R14.2, X2.3; also elsewhere on the board
BTN_STOP: R10.1, R15.2, X2.5; also elsewhere on the board
BTN_UP: R12.1, R13.2, X2.1; also elsewhere on the board
DHT22_DATA: R3.1, U1.DATA; also elsewhere on the board
GND: C12.2, C13.2, Q1.2 (S), R6.1, R8.1, R13.1, R14.1, R15.1, R23.1, T1.2 (E), T3.C, U1.GND, U7.P$3 (GND), X2.2, X2.4, X2.6, X3.4, X3.6; also elsewhere on the board
LIGHT_GATE_PRERES: R1.1, T2.2 (E), T3.E
LIGHT_OUT: Q1.3 (D), X4.2
LIGHT_PWM: R5.1; also elsewhere on the board
LIGHT_PWM_BASE: R5.2, T1.1 (B), TP10.TP
LIGHT_PWM_EMITTER: R2.1, R4.1, T1.3 (C)
LIGHT_PWM_TOTEM: R4.2, T2.1 (B), T3.B
LIGHT_SENSOR: R23.2, U8.2 (E); also elsewhere on the board
LIGHT_SENSOR_VDD: C12.1, C13.1, R22.2, U7.P$2 (VDD)
LIGHT_VGATE: Q1.1 (G), R1.2, TP9.TP
MAIN_DOOR: R6.2, R7.1, X3.3; also elsewhere on the board
NESTING_BOX: R8.2, R9.1, X3.5; also elsewhere on the board
SCL: U7.P$1 (SCL); also elsewhere on the board
SDA: U7.P$4 (SDA); also elsewhere on the board

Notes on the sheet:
DOOR SENSORS
PUSH BUTTON INPUTS
TEMP/HUMIDITY SENSOR
LIGHT SENSOR OPTION 1
LIGHT SENSOR OPTION 2
COOP LIGHT

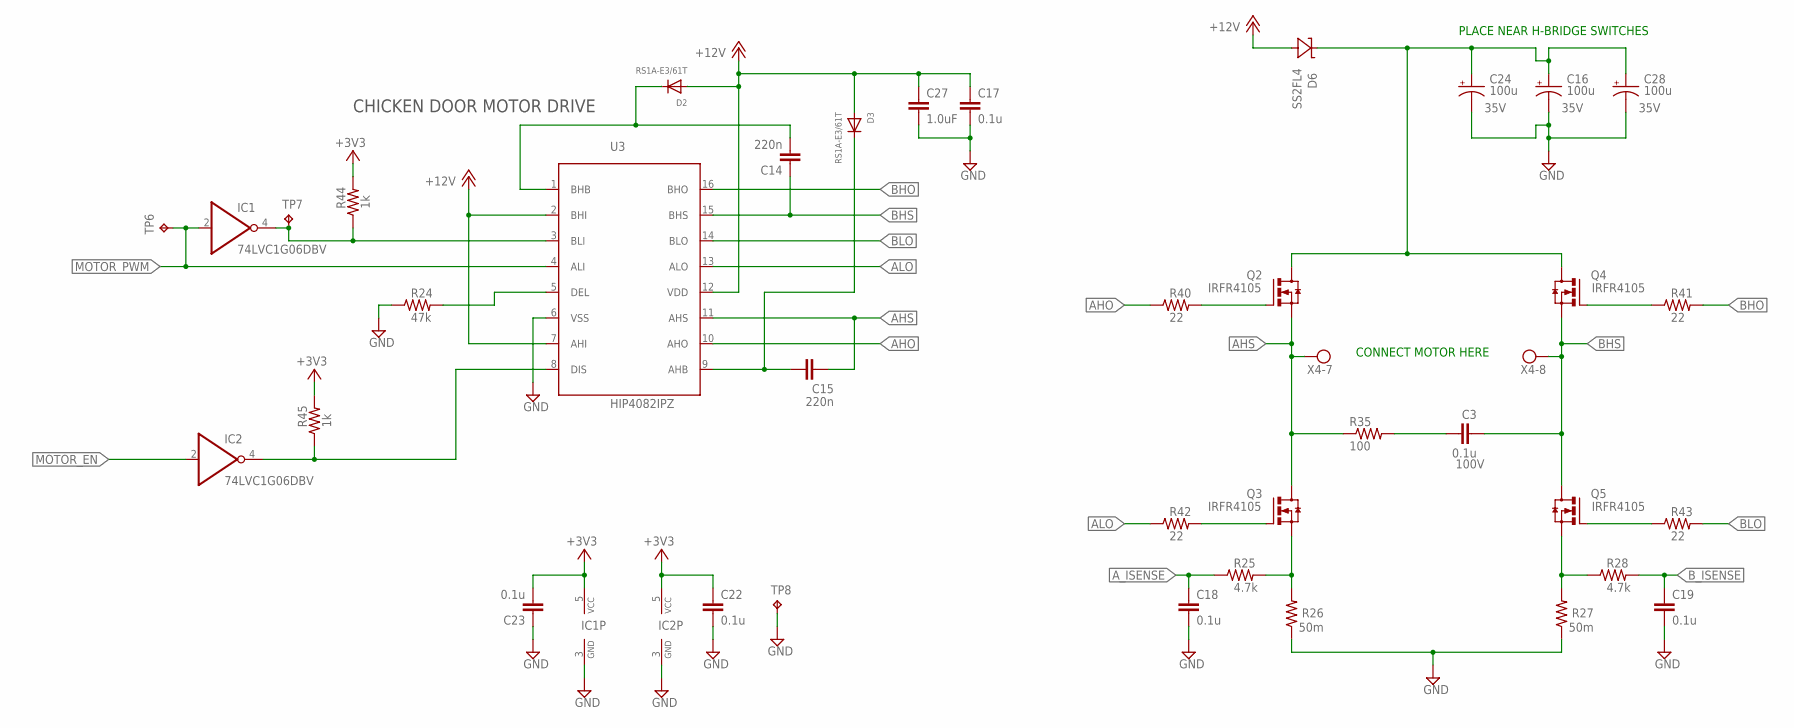
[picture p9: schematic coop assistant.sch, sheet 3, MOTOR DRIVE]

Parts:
C3: 0.1u; C0805; VOLTAGE 100V
C14, C15: 220n; 0805
C16, C24, C28: 100u; CAPPRD350W60D800H1200B; VOLTAGE 35V
C17, C18, C19, C22, C23: 0.1u; 0603
C27: 1.0uF; 0805
D2, D3: RS1A-E3/61T; SMADIODE
D6: SS2FL4; SMF
IC1, IC2: 74LVC1G06DBV; SOT23-5
Q2, Q3, Q4, Q5: IRFR4105; TO252
R24: 47k; R0805
R25, R28: 4.7k; R0805
R26, R27: 50m; R2512
R35: 100; R2512
R40, R41, R42, R43: 22; R0805
R44, R45: 1k; R0805
TP6, TP7, TP8: TPTP15SQ; TP15SQ
U3: HIP4082IPZ; DIP762W53P254L1969H508Q16B
X4: MKDSN1,5/8-5,08

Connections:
+3V3: C22.1, C23.2, IC1.5 (VCC), IC2.5 (VCC), R44.2, R45.2; also elsewhere on the board
+12V: C17.1, C27.1, D2.A, D3.A, D6.A, U3.2 (BHI), U3.7 (AHI), U3.12 (VDD); also elsewhere on the board
+12V_MOTOR: C16.POS (+), C24.POS (+), C28.POS (+), D6.K (C), Q2.3 (D), Q4.3 (D)
/MOTOR_EN: IC2.4 (O), R45.1, U3.8 (DIS)
/MOTOR_PWM: IC1.4 (O), R44.1, TP7.TP, U3.3 (BLI)
AHO: R40.1, U3.10 (AHO)
AHO_G: Q2.1 (G), R40.2
AHS: C15.2, Q2.2 (S), Q3.3 (D), R35.1, U3.11 (AHS), X4.7
ALO: R42.1, U3.13 (ALO)
ALO_G: Q3.1 (G), R42.2
ALS: Q3.2 (S), R25.2, R26.2
A_ISENSE: C18.1, R25.1; also elsewhere on the board
BHO: R41.2, U3.16 (BHO)
BHO_G: Q4.1 (G), R41.1
BHS: C3.2, C14.1, Q4.2 (S), Q5.3 (D), U3.15 (BHS), X4.8
BLO: R43.2, U3.14 (BLO)
BLO_G: Q5.1 (G), R43.1
BLS: Q5.2 (S), R27.2, R28.1
B_ISENSE: C19.1, R28.2; also elsewhere on the board
GND: C16.NEG (-), C17.2, C18.2, C19.2, C22.2, C23.1, C24.NEG (-), C27.2, C28.NEG (-), IC1.3 (GND), IC2.3 (GND), R24.1, R26.1, R27.1, TP8.TP, U3.6 (VSS); also elsewhere on the board
HIP4082_BOOTA: C15.1, D3.C, U3.9 (AHB)
HIP4082_BOOTB: C14.2, D2.C, U3.1 (BHB)
HIP4082_DLY: R24.2, U3.5 (DEL)
MOTOR_EN: IC2.2 (I); also elsewhere on the board
MOTOR_PWM: IC1.2 (I), TP6.TP, U3.4 (ALI); also elsewhere on the board
MOTOR_SNUB_RC: C3.1, R35.2

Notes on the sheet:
CHICKEN DOOR MOTOR DRIVE
PLACE NEAR H-BRIDGE SWITCHES
CONNECT MOTOR HERE

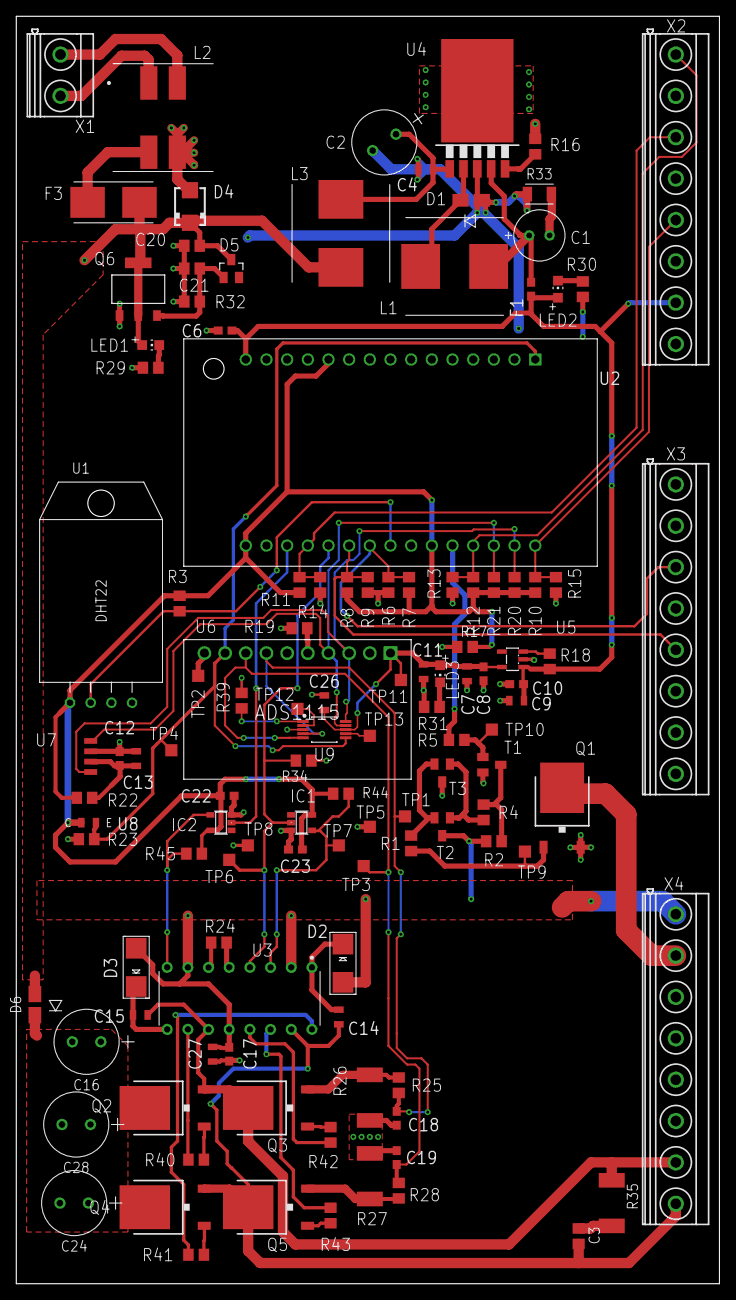
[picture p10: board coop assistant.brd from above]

Board: 2 copper layers, 86.4 x 155.7 mm, 119 parts (0 on the bottom side), 63 nets.

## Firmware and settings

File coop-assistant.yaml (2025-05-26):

# D0/GPIO16 - Push Button Stop
# D1/GPIO5  - I2C SCL
# D2/GPIO4  - I2C SDA
# D3/GPIO0  - Push Button Up
# D4/GPIO2  - Coop Light PWM
# D5/GPIO14 - DHT Sensor
# D6/GPIO12 - Main Door
# D7/GPIO13 - Nesting Box Lid
# D8/GPIO15 - Motor PWM
# RX/GPIO3  - Push Button Down
# TX/GPIO1  - Motor Drive Enable

esphome:
  name: coop-assistant
  
  libraries:
    - "Wire"
    - "SPI"
    - "Adafruit BusIO"

esp8266:
  board: nodemcuv2
  restore_from_flash: true

# Enable logging
logger:
  level: DEBUG
  logs:
    ads1115: INFO
    sensor: INFO

# Enable Home Assistant API
api:
  services:
    - service: set_auto_open_arm
      then:
        - script.execute: auto_open_arm
        
    - service: set_auto_open_disarm
      then:
        - script.execute: auto_open_disarm

    - service: set_auto_close_arm
      then:
        - script.execute: auto_close_arm
        
    - service: set_auto_close_disarm
      then:
        - script.execute: auto_close_disarm

ota:
  platform: esphome
  password: !secret ota_pass 

wifi:
  ssid: !secret wifi_ssid
  password: !secret wifi_password
  use_address: 10.0.101.123

  # Enable fallback hotspot (captive portal) in case wifi connection fails
  ap:
    ssid: "Coop-Assistant Fallback Hotspot"
    password: !secret ap_pass

captive_portal:

i2c:
  sda: GPIO4
  scl: GPIO5
  scan: false
  
ads1115:
  - address: 0x48
  
globals:
  - id: auto_open_armed
    type: boolean
    restore_value: yes
    initial_value: "false"
    
  - id: auto_close_armed
    type: boolean
    restore_value: yes
    initial_value: "false"
    
time:
  - platform: homeassistant
    id: ha_time
    timezone: 'America/Chicago'
    
    on_time_sync:
      then:
        - logger.log: "Synchronized system clock"
    
    on_time:
      # If automatic door opening is configured, arm it at 6am 
      - seconds: 0
        minutes: 0
        hours: 6
        then:
          - if:
              condition:
                lambda: 'return id(door_mode).state == "automatic";'
              then:
                - script.execute: auto_open_arm
              
      # If automatic door opening is configured, confirm at 8am if it actually opened
      - seconds: 0
        minutes: 0
        hours: 8
        then:
          - if:
              condition:
                and:
                  - lambda: 'return id(door_mode).state == "automatic";'
                  - lambda: 'return id(auto_open_armed) == true;'
              then:
                - script.execute: auto_open_disarm
                - logger.log: 'Open Armed Door (Timeout)'
                - homeassistant.event:
                    event: esphome.coop_assistant_automatic_door
                    data:
                      status: 'Open Armed Door (Timeout)'
                - cover.open: chicken_door
              
      # If automatic door closing is configured, arm it at 5 pm
      - seconds: 0
        minutes: 0
        hours: 17
        then:
          - if:
              condition:
                lambda: 'return id(door_mode).state == "automatic";'
              then:
                - script.execute: auto_close_arm

      # If automatic door closing is configured, confirm at 9pm if it actually closed
      - seconds: 0
        minutes: 0
        hours: 21
        then:
          - if:
              condition:
                and:
                  - lambda: 'return id(door_mode).state == "automatic";'
                  - lambda: 'return id(auto_close_armed) == true;'
              then:
                - script.execute: auto_close_disarm
                - logger.log: 'Close Armed Door (Timeout)'
                - homeassistant.event:
                    event: esphome.coop_assistant_automatic_door
                    data:
                      status: 'Close Armed Door (Timeout)'
                - cover.close: chicken_door
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

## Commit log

2022-01-13 Adding Rev A PCB files and datasheets
    [Bill of Materials.xlsx, coop assistant.brd, coop assistant.csv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]
2022-02-02 Update ESPHome config with custom component for illuminance sensor
2022-02-12 Update with some improvements to illuminance sensor
2022-02-13 Adding Rev B PCB files
    [Bill of Materials.xlsx, coop assistant.brd, coop assistant.sch]
2022-08-24 Rev B PCB Update
    [Bill of Materials.xlsx, coop assistant.brd, coop assistant.sch]

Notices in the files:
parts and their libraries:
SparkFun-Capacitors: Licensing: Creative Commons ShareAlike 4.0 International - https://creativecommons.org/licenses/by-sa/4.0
